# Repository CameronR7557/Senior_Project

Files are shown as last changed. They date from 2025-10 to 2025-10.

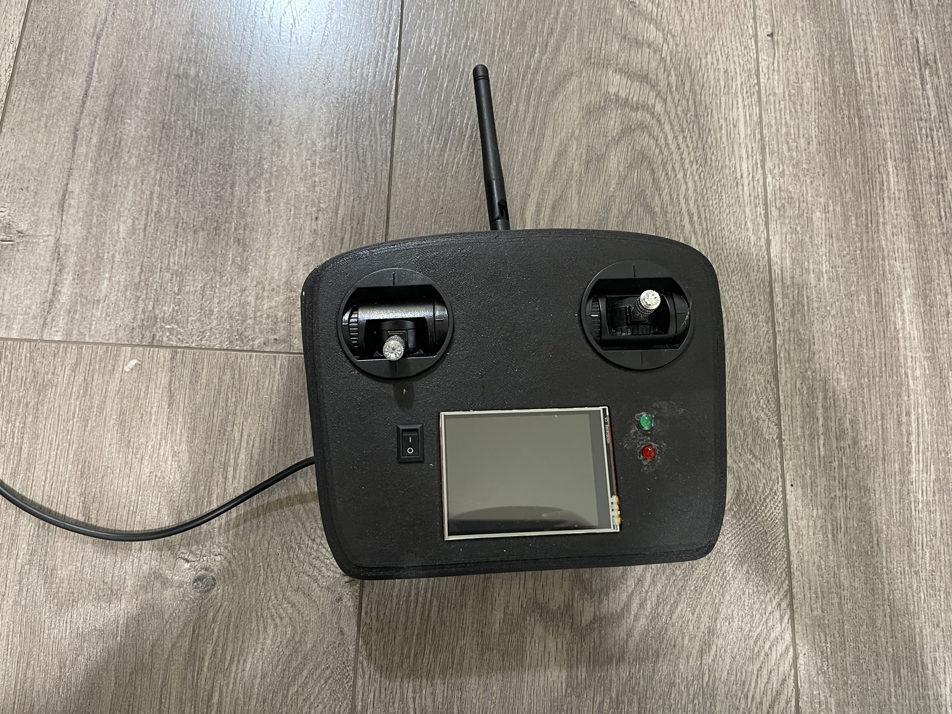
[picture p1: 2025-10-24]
Remote Control.jpg

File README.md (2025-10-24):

This repo contains the code, schematics, diagrams, etc. from my senior project in 2024. In this project I researched and prototyped a quadcopter and remote control. The goal of this project was to learn about quadcopters, LiDAR, and collision avoidance algorithms. The quadcopter used a 2D LiDAR to determine its distance from obstacles and then used those distances to update the motor control and attempt to avoid them.
It is important to note that, while I certainly learned a lot from this project, due to time constraints I was not able to get the flight controller tuned before the project ended, and was not able to test the collision avoidance algorithm on the drone in flight since the drone could not stay in the air without flipping for more than a few seconds. 

This was my planned schedule for this project.
Schedule

Below is the parts list for this project.
Parts List

This is the assembed quadcopter.

Quadcopter

This is the assembled remote control.

Remote Control

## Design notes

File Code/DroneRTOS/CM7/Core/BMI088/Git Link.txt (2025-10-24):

https://github.com/bao-eng/BMI088-STM32/tree/master

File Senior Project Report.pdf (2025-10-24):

# Senior Project Report: Collision Avoidance Drone

2024

Submitted to: Ganghee Jang

Submitted by: Cameron Robinson

June 13, 2024

Version 1.6

Submitted in fulfillment of requirements for Embedded Senior Project (CST 473), Oregon Institute of Technology.

©2024, Cameron Robinson, All Rights Reserved.

## Revision History

Version | Date | Editor | Changes
1.0 | 5/26/23 | Cameron Robinson | Initial submission for Spring of 2023
1.1 | 6/14/23 | Cameron Robinson | Revised submission for Spring of 2023
1.2 | 11/12/23 | Cameron Robinson | Updated report for middle of Fall 2023
1.3 | 12/12/23 | Cameron Robinson | Updated report for end of Fall 2023
1.4 | 2/28/24 | Cameron Robinson | Updated report for middle of Winter 2024
1.5 | 3/17/24 | Cameron Robinson | Updated report for end of Winter 2024
1.6 | 6/13/24 | Cameron Robinson | Added final sections. Revised all other sections.

## Legal Notice

The following parties have reviewed and agreed to the terms presented in this proposal.

Student:

______________________________________________________

Name | Date

Professor:

______________________________________________________

Name | Date

## Abstract

The following paper is a report on the previously proposed project to design and build a collision

avoidance quadcopter drone. Development for this project began in fall 2023 and will end in spring

2024. The estimated non-recurring costs for one engineer to work on this project 15-20 hours a week for

33 weeks is about $26,717.14 ($45.00/hour and $729.64for parts). In addition to skills such as time

management and researching, this project will require the engineer to be able to design an embedded

system; code in C; be able to design and print 3D models; and be able to design and build electric

circuits.

The purpose of this project is to research LiDAR, drone, and autonomous vehicle technologies by

creating a project that incorporates all three of them. This project is a quadcopter drone that uses a

LiDAR sensor to detect obstacles in the surrounding environment. If the drone senses it is going to

collide with any obstacles, it will automatically avoid it. The project will also include a remote control to

manually control the drone. This project is not intended to solve a particular problem or become a

sellable product.

The following paper will include details related to the major components of the project. These details

include system design, hardware, software, project requirements, testing results, and encountered

problems.

Overall, the project turned out well, and nearly all the requirements were completed and tested.

Unfortunately, the drone is still unable to fly due to destabilization in the flight controller. Despite this, a

lot was learned about collision avoidance algorithms, quadcopters, LiDARs, and flight control software

throughout the development of this project.

## Table of Contents

Inertial Measurement Unit | 22
Extended Kalman Filter | 23
PID Controllers | 23
Electronic Speed Controller | 23
BLDC Motors | 24
Project Housing | 24
Hardware | 25
Part Matrices | 26
Hardware Components | 32
Software | 40
Remote Control | 40
Quadcopter | 46
Encountered Problems | 58
Assembled Project | 59
Testing | 61
Conclusion | 63
Glossary | 65
Appendix | 66
References | 77

## List of Figures

Figure 1: Project Timeline | 8
Figure 2: Remote Control System Block Diagram | 20
Figure 3: Drone System Block Diagram | 21
Figure 4: Controller Shell | 24
Figure 5: Quadcopter Frame | 25
Figure 6: IMU Specifications Adapted from [15] | 35
Figure 7: Temperature and Pressure Conversion Equations Adapted from [13] | 36
Figure 8: Controller Software Diagram | 40
Figure 9: Blink Task Code | 41
Figure 10: ADC Conv. Complete ISR UML | 42
Figure 11: LCD Display Task UML | 43
Figure 12: LCD Task Code | 43
Figure 13: Radio RX/TX ISR UML | 44
Figure 14: Controller Radio ISR Code | 45
Figure 15: Radio Write Ack Payload Function | 45

Figure 16: Drone Software Diagram | 46
Figure 17: 2D LiDAR Task UML | 47
Figure 18: LiDAR Get Measurements Function | 48
Figure 19: Radio RX ISR | 49
Figure 20: Radio TX Task UML | 49
Figure 21: Drone Radio TX Task Code | 50
Figure 22: Collision Avoidance Algorithm Diagram | 51
Figure 23: Collision Avoidance Task UML | 52
Figure 24: Collision Avoidance Task Code | 53
Figure 25: Read IMU Task | 54
Figure 26: Read Pressure Sensor Task | 55
Figure 27: Read Pressure Sensor Task Code | 55
Figure 28: Height Task UML | 56
Figure 29: PID Update Task UML | 58
Figure 30: Assembled Quadcopter Drone | 59
Figure 31: Assembled Controller - Top-Down | 60
Figure 32: Assembled Controller – Front | 60
Figure 34: Controller Wiring Schematic | 66
Figure 35: Drone Wiring Schematic | 67
Figure 35: LiDAR Data Parsing Function | 68
Figure 36: LiDAR CRC Function | 69
Figure 37: ADC Conversion Complete ISR | 70
Figure 38: PID Control Equations. Adapted from [5] | 71
Figure 39: IMU Task | 72
Figure 40: Drone Radio RX ISR | 73
Figure 41: Rangefinder Functions | 74
Figure 42: Init CA and Obstacle Detection Functions | 75
Figure 43: Obstacle Avoidance Function | 75
Figure 44: Measure Height Task Code | 76

## List of Tables

Table 1: Estimated Engineering Costs | 9
Table 2: Estimated Cost of Parts | 10
Table 3: Potential MCUs | 27
Table 4: Potential IMUs | 27
Table 5: Potential Pressure Sensors | 28
Table 6: Potential ESCs | 28
Table 7: Potential Radio Transceivers | 29
Table 8: Potential LCDs | 29
Table 9: Potential Rotating LiDARs | 30
Table 10: Potential BLDC Motors | 31
Table 11: Potential LiPo Batteries | 32
Table 12: Potential Distance Measuring Units | 32

## Project Management

### Project Timeline

Figure 1, pictured below, is the timeline of the collision avoidance quadcopter drone project. The blue

tasks will be done by the end of winter 2024. The purple tasks represent project stretch goals; they may

or may not be implemented during spring of 2024. There were a couple of delays throughout the

development of this project. The first delay was due to the IMU data not being filtered enough, which

caused the accelerometer readings to spike to very large values. The second, and most significant delay,

was due to the drone’s flight controller destabilizing and causing the drone to oscillate out of control.

Due to these delays, it is unlikely that the stretch goals will be implemented during spring term.

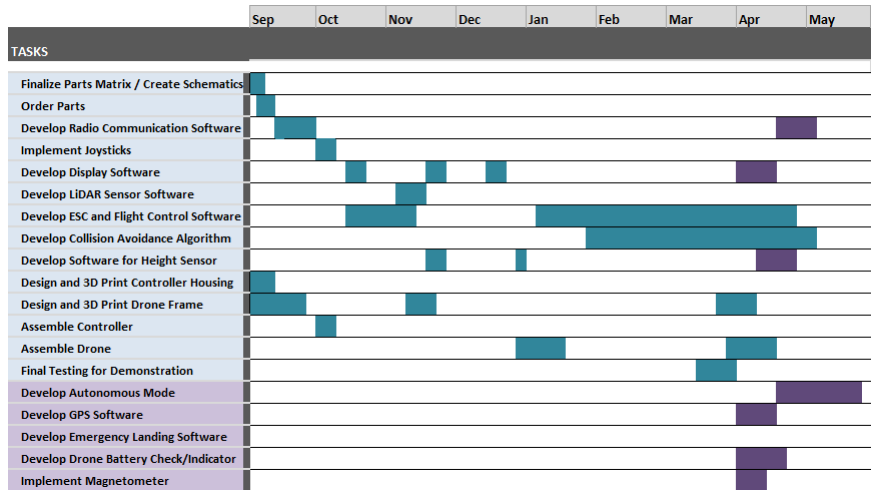
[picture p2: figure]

Figure 1: Project Timeline

### Non-Recurring Costs

The cost of one engineer working on this project for 15 – 20 hours a week at $45.00 per hour is about

$787.5 dollars per week. The total amount of time for initial development is about 22 weeks (fall 2023

and winter 2024), which results in a cost of $17,325.00. The total time for testing and developing

additional features is about 11 weeks (Spring 2024) which results in an additional cost of $8,662.50.

Table 1 shows the estimated engineering costs for fall, winter, and spring, as well as the total estimated

engineering cost. Table 2 lists all the parts and materials used in the project and how much they cost.

The total estimated cost of all parts is $729.64. Overall, the total estimated non-recurring cost for

research and development over a 33-week period is $25,987.50 in engineering costs and $729.64 in

materials, which results in a total cost of $26,717.14.

Table 1: Estimated Engineering Costs

Reason | Cost ($)
Fall Term Research and Development (11 Weeks) | 8,662.50
Winter Term Development (11 Weeks) | 8,662.50
Spring Term Testing and Development (11 Weeks) | 8,662.50
Total: | 25,987.50
Part Name | Quantity | Unit | Total Part Cost ($)
NUCLEO-H755ZI-Q | 2 | pcs | 58.00
Grove 6-Axis IMU (BMI088) | 1 | pc | 29.04
ICP-10111 Pressure Sensor | 1 | pc | 7.90
F405 V3 50A 4in1 ESC | 1 | pc | 49.99
NRF24L01+PA+LNA w/ Breakout Adapter | 3 | pcs | 13.99
ILI9341 2.8" SPI TFT LCD | 1 | pc | 16.39
FHL-LD19 | 1 | pc | 84.34
2212 920KV BLDC Motor | 4 | pcs | 39.99
HRB 4S LiPo | 1 | pc | 37.49
LIDAR07 | 1 | pc | 19.99

### Project Tools

GitHub, Word, and Excel will be the primary project management tools used in this project. GitHub will

be used for source control and storing documentation, and diagrams. Word will be used for

documentation development and storing research notes. Excel will be used to create graphs, tables, and

charts (such as Gantt charts) that will be used for project management.

Onshape, a CAD program, will be used for designing the 3D parts for both the drone and controller. As a

student, Onshape is free to use, so using it does not add to the cost of the project.

Other tools that will be used throughout this project include Dia and KiCad. Dia will be used to create

project diagrams (such as system block diagrams), and KiCad will be used to make wiring schematics.

Other software tools, such as IDEs, are discussed under the ‘Software’ heading in the ‘System

Description’ section.

1045 Propellers | 4 | pcs | 15.99
NylonG | 1000 | g | 128.00
NylonX | 500 | g | 58.00
Rosin Core Lead-Free Solder | 100 | g | 19.99
URGENEX 7.4V LiPo | 2 | pcs | 19.99
SCIGRIP Acrylic Plastic Cement | 5 | fl. oz. | 14.35
14 AWG Silicone Wire | 50 | ft | 19.98
Dupont Wires | 120 | pcs | 6.98
LM7805 | 2 | pcs | 8.29
Rocker Switch | 1 | pc | 6.99
Joystick | 2 | pcs | 31.98
LEDs | 2 | pcs | 0.05
330-Ohm Resistors | 2 | pcs | 0.06
LM2596 Buck Converter | 4 | pcs | 13.99
1045 Carbon Fiber Propellers | 8 | pcs | 27.88
Total Estimated Parts Cost | | | 729.64

Table 2: Estimated Cost of Parts

### Change Management Procedure

Any changes to this project after the beginning of fall 2023 will require the engineer to submit a request

for that change in the form of an Engineering Change Order (ECO). The ECO form should contain

information about what change is being made, why it is being made, and what will be affected by the

change. The engineer must submit the ECO and get it approved by their supervisor. Changes to the

project may require additional forms to be filled out or previously submitted work to be revised or

recreated.

### Status Report

The engineer in charge of the project will be required to submit a weekly memo to their supervisor. This

memo will contain:

- Project progress
- Updates to the timeline
- Problems encountered
- Goals for the following week
- Any major problems or setbacks

Should the engineer fail to submit the weekly memo, there will be repercussions.

### Skills

This project will require the following skills:

- Programming in C
- Designing system diagrams and wiring schematics
- Soldering
- Designing and printing 3D models

- Researching and understanding complex topics (drone flight, PID control, collision avoidance

algorithms, etc.)

- Managing time and workload
- Ability to solve complex problems
- Ability to test hardware and software on embedded systems

## Conceptual Overview

### Introduction

Technology tends to advance very quickly, with new technologies constantly being released and the

applications of existing technologies expanding. This is also the case with technologies such as LiDAR,

drones, and autonomous vehicles. Fields that LiDAR is used in include agriculture, construction,

geographical mapping, and autonomous vehicles. Drones, in addition to being used in agriculture and

geographical mapping, are also used in weather and storm monitoring, cinematography, and much

more. Autonomous vehicle technologies like autonomous delivery drones and cars are also constantly

advancing.

The project outlined in this paper is a research project that combines these three technologies: drones,

LiDAR, and autonomous vehicle algorithms. The purpose of this project is to learn about these

technologies and gain a better understanding of them. Although this project is not going to solve a

particular solution in a completely unique way, it is still a valuable project because drones, LiDAR and

autonomous vehicles are advancing technologies with a multitude of applications.

### Intended Audience

Since my project is a research project, my primary audience is academics. Particularly, any person

wanting to learn more about LiDAR, drones, and collision avoidance algorithms.

### Proposed Project

This document is a proposal to create a collision avoidance quadcopter drone. The main components of

this project are a quadcopter, remote control, and collision avoidance algorithm. For collision avoidance

the drone will use a 2D 360-degree rotating LiDAR. This module will sit on the drone and constantly

measure the distance between the drone and obstacles in the surrounding environment. These distance

measurements will be used by collision avoidance algorithms to adjust the drone’s flight to avoid any

obstacles it will collide with. The remote control will be used to manually control the flight of the drone

with two joysticks.

### Existing Solutions

Quadcopters

There are multiple collision avoidance drones currently on the market. The cost of these drones tends to

range from around $300.00 to well over $1000.00. Two example drones are the DJI Air 2S [1] and the

EXO X7 Ranger PLUS [2]. Although neither of the drones’ product pages specify what kind of sensor

(LiDAR, ultrasonic, etc.) each drone uses, neither one appears to use a 2D 360-degree rotating LiDAR

sensor. Additionally, although the EXO X7 Ranger PLUS does have 360-degree obstacle detection, it

avoids obstacles by simply stopping the drone, rather than flying around the obstacle.

Collision Avoidance Algorithm

The collision avoidance algorithm developed throughout this project shares some similarities to the

dynamic window approach (DWA) [21]. The DWA is a collision avoidance algorithm that analyzes a small

area around a robot and determines the path the robot should take by considering its velocity and the

location of surrounding obstacles. The area around the robot that is analyzed, the dynamic window, is

determined by how far the robot can travel given its restrictions and velocity. This algorithm is an

example of a dynamic collision avoidance algorithm because it reacts to obstacles without prior knowledge of the environment. In this project, the collision avoidance algorithm will be a dynamic

algorithm, however, it will not implement any form of path planning like the DWA.

Flight Controller

There are many methods of implementing flight controllers for quadcopters, however, one of the most

common methods uses a 6-axis inertial measurement unit (IMU) and PID controllers. Often, the PID

controllers are implemented to control the angle and angular rate of the quadcopter.

The IMU data is used as measurement inputs into the PID controllers. Measurement inputs represent

the current state of the drone. For example, a flight controller could have three angular rate controllers

(one for roll rate, pitch rate, and yaw rate), where each controller receives its respective angular rate

measurement from the IMU’s 3-axis gyroscope that represents how fast the drone is currently rotating

on that specific axis.

The PID controllers also receive a setpoint value, which represents the state they are controlling to. In

most quadcopters, the setpoint for each axis is determined by the position of the joysticks on the remote

control. PID controllers calculate output values based on an error term, which is the difference between

the setpoint and the measurement (the difference between the current state and the desired state).

These outputs are used in motor-mixing equations to calculate throttle values for each of the

quadcopter’s motors that will get the drone from its current state to its desired state.

### Deliverables

The final deliverables of this project will be a mostly functional remote control and quadcopter drone as

specified in the ‘Requirements’ section. The controller will control the flight of the drone with two

joysticks. The drone will incorporate a LiDAR module which it will use to detect obstacles in the

surrounding environment. The drone will attempt to avoid obstacles it is going to collide with. The

project should be mostly functional by the end of spring 2024.

## Requirements

The following is a list of requirements for the collision-avoidance quadcopter drone. These requirements

define what the final project should be able to do by the end of Spring 2024. Under each requirement is

a list of the identification numbers of codependent requirements. The listed codependent requirements

are requirements that are essential to the completion of the requirement they are listed under.

1. The project will have a quadcopter drone with four propellers, each rotating on a brushless DC

motor.

a. The motors and propellers will be used by the drone to maneuver in the air.
b. The drone will be custom-built for this project.

Codependent requirements: 3, 5.

2. The project shall have a remote control to operate the drone from a distance.
a. The controller will be custom-built for this project.

Codependent requirements: 1, 3, 4, 7.

3. The drone and controller will both have their own microcontrollers.
a. Each microcontroller shall be fast enough to process all needed data and respond to

external events in near real-time.

Codependent requirements: 1, 2, 5.

Justification: This project will use microcontrollers for both the controller and drone since most

commercial quadcopters use them. Near real-time responses will be essential for avoiding obstacles.

4. The drone and controller will communicate via radio.
a. May be able to communicate from 50 feet away.

b. Shall be able to communicate from 25 feet away.

Codependent requirements: 1, 2, 3, 5.

5. The drone and controller will be powered by batteries.
a. The batteries will be rechargeable.
b. The drone may be able to fly for 15 minutes or more.

Codependent requirements: 1, 2.

6. The controller will have an LCD screen to display relevant information related to the drone.
a. The LCD screen shall display indications of obstacles around the drone.
b. The LCD screen may display the drone’s GPS location data.
c. The LCD screen shall refresh at least 15 times per second.
d. The LCD screen may indicate quadcopter battery level.

Codependent requirements: 2, 4, 8.

7. The controller will have two joysticks.
a. One joystick will control the throttle and yaw of the drone.
b. One joystick will control the pitch and roll of the drone.
c. The values of each joystick will be read through an ADC on the controller’s MCU.

Codependent requirements: 1, 2, 3, 4.

8. The drone shall use a rotating LiDAR module for obstacle detection.
a. LiDAR module will be active while the drone is in flight.
b. The module shall detect objects at least three meters away.
c. The module may detect objects up to twelve meters away.

Codependent requirements: 1, 3, 5.

Justification: One of the main goals of this project is to learn about LiDAR, so while something like an

ultrasonic sensor may fulfill a similar purpose, a LiDAR is more in line with the goals of this research

project. The LiDAR should be able to detect obstacles at least three meters away since that will

hopefully give the drone enough time to stop or avoid it, however, due to restrictions on LiDAR

resolution, some small objects may be missed even at distances closer than three meters.

9. The drone shall use an inertial measurement unit (IMU) to increase flight stability.
a. The IMU data shall be used to adjust the speed of the drone’s motors.
b. The IMU will have at least a 3-axis gyroscope and 3-axis accelerometer.

Codependent requirements: 1, 3, 5.

10. The drone shall attempt to avoid detected obstacles if it senses it is going to collide with any.
a. Results from object detection algorithms shall be used along with drone movement data

(i.e., from IMU and joysticks) to determine if the drone will collide with an obstacle.

b. The movement of the drone shall be adjusted to prevent collision with obstacles.

Codependent requirements: 1, 2, 3, 4, 5, 7, 8, 9.

11. The drone may have an autonomous mode.
a. In autonomous mode, the drone may take off, fly to a specified location, avoid obstacles,

and land on its own.

b. Autonomous mode may be turned on and off with a switch on the controller.

Codependent requirements: 1, 3, 5, 8, 9, 10, 13, 14.

Justification: As discussed later in the ‘Part Matrices’ section, the quadcopter will use an H7-series

STM32 microcontroller. Many commercial quadcopter drones, even those with GPS return-home functions, use F4 or F7-series STM32 MCUs. The F-series MCUs have less than half the maximum

clock speed of the H7-series, which makes it seem feasible that an autonomous mode could be

implemented in this project.

12. The drone shall have a semi-autonomous mode.
a. In semi-autonomous mode, the drone’s flight shall be controlled with the controller.
b. In semi-autonomous mode, the drone shall automatically detect and attempt to avoid

obstacles it senses it will collide with.

c. Semi-autonomous mode may be turned on and off with a switch.

Codependent requirements: 1, 2, 3, 4, 5, 7, 8, 9.

13. The drone will use a distance measuring module to measure its distance from the ground.
a. The module will either be a LiDAR or ultrasonic ranging module.
b. The module’s distance measurements may be used to make the drone hover some

distance above the ground.

c. The module’s distance measurements may be sent to the controller to display on the

LCD.

Codependent requirements: 1, 3, 5.

Justification: Knowing how far the drone is from the ground will allow for better obstacle avoidance

since the drone may need to know if it can fly up or down to avoid an obstacle. Either a LiDAR or

ultrasonic ranging module could fulfill this purpose.

14. The drone will use a pressure sensor to estimate its distance from the ground.
a. The pressure sensor may be used in conjunction with the distance sensor to get a more

accurate measurement of how far the drone is from the ground.

Codependent requirements: 1, 3, 5.

Justification: A pressure sensor fulfills the same role as the distance sensor mentioned in

requirement 13, however, it can measure much further distances from the ground than the distance

measuring module. If used alongside the distance measuring module, the estimated distance from

the ground should be more accurate than just using one or the other.

15. The drone may use a GPS module to receive data related to its own location.
a. GPS data may be used to allow the drone to fly to a specific location.

Codependent requirements: 1, 3, 5.

16. The drone may have an emergency landing feature where the drone will automatically land on

the ground.

a. An emergency landing may initiate when the battery reaches a certain level.
b. An emergency landing may initiate if the drone loses connection with the controller.

Codependent requirements: 1, 3, 5.

17. Most parts of the drone and controller’s housing shall be 3D printed.

Codependent requirements: 1, 2.

## System Description

The following section is an overview of the system designs for remote control and drone, which are

designed to meet the above requirements.

### Remote Control

Figure 2, pictured below, illustrates the system block diagram for the remote control. The main

components in the controller are the analog to digital converter (ADC), radio transmitter (Radio TX),

radio receiver (Radio RX), display, and the two joysticks.

ADC and Radio TX:

The ADC is used to read the positions of the two connected joysticks. In total, the ADC will read four

values from the joysticks; throttle and yaw from one joystick, and pitch and roll from the other. These

values are used to control the angular velocity of the drone’s four motors. Once the data is collected

from the joysticks, it is sent to the radio transmitter which will transmit it to the drone’s radio receiver.

Radio RX and LCD

The radio receiver receives LiDAR data from the drone and sends it to the LCD, which will display

detected obstacles within a certain distance from the drone.

Figure 2: Remote Control System Block Diagram

### Quadcopter Drone

Figure 3, shown below, illustrates the system block diagram for the drone. The major components

include the radio transmitter and receiver, 2D LiDAR, rangefinder, inertial measurement unit, extended

Kalman filter, PID controllers, brushless DC (BLDC) motors, electronic speed controller (ESC), pressure

sensor, and collision avoidance algorithm.

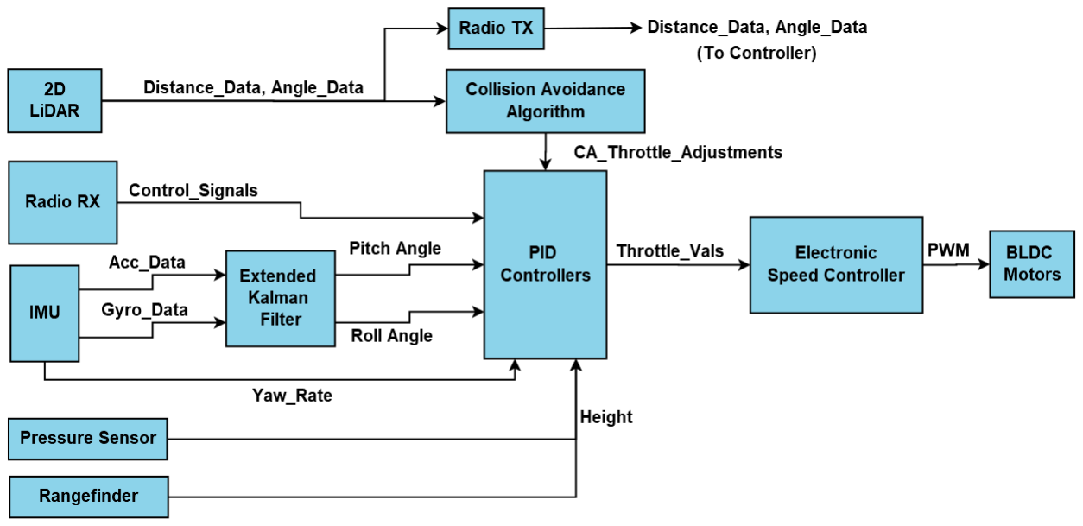
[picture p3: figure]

Figure 3: Drone System Block Diagram

2D LiDAR

The 2D LiDAR module is a 360-degree rotating distance sensor that measures distances between the

drone and obstacles in the surrounding environment. This distance data is sent to the Radio TX and

Collision Avoidance Algorithm blocks.

Rangefinder and Pressure Sensor

Both the rangefinder and pressure sensor perform the same function: they measure the distance

between the drone and the ground. This data will potentially be used to allow the drone to hover a

certain height above the ground. Not only does measuring the distance to the ground with two different

sensors help verify that the measurements are correct, but each sensor also helps account for the

other’s weaknesses. The rangefinder is only accurate when measuring certain types of materials and can

only measure up to a maximum distance. On the other hand, the pressure sensor is not restricted by distance from the ground, however, its measurements are based on the air pressure at sea level, so it

does not necessarily know how far away the ground is.

Radio TX

The radio transmitter sends the LiDAR angles and distance measurements to the remote control.

Collision Avoidance Algorithm

The collision avoidance algorithm for this project uses the 2D LiDAR data to detect obstacles in the

drone’s surroundings. This algorithm is divided into three steps: obstacle detection, hazard assessment,

and obstacle avoidance.

Obstacle detection analyzes the LiDAR data to determine the distance and direction of obstacles around

the drone. The hazard assessment step determines which obstacles the drone is most likely to collide

with and outputs values that prioritizes avoiding those obstacles. Lastly, obstacle avoidance uses the

results from the hazard assessment and obstacle detection stages to determine adjustment values for

the drone’s motors that will allow it to avoid the obstacles.

Radio RX

The radio receiver receives joystick position data from the remote control. This data is sent directly to

the PID Controllers block.

Inertial Measurement Unit

The inertial measurement unit (IMU) is a sensor that detects linear acceleration and angular velocity.

This module is essential to the flight controller since it provides angle and angular rate measurements to

the PID controllers. Angular velocity is measured with a 3-axis gyroscope and linear acceleration is

measured with a 3-axis accelerometer. The gyroscope and accelerometer readings are sent to the

Extended Kalman Filter block. The gyroscope yaw reading is also sent directly to the PID Controllers

block.

Extended Kalman Filter

The extended Kalman filter is implemented in software and uses the gyroscope and accelerometer data

to estimate the quadcopter’s roll and pitch angles. The roll and pitch angle estimations are sent to the

PID Controllers block and are used for controlling and the drone’s flight.

PID Controllers

The PID Controllers block represents software algorithms for controlling drone flight and stabilization.

This block takes in the joystick data, collision avoidance results, IMU data, and the drone’s distance from

the ground. This data is used to calculate how fast each of the drone’s four motors should be spinning to

avoid obstacles or move in the direction specified by the joystick values. Once the throttle for each

motor is calculated, the values are sent to the ESC through a protocol called DSHOT.

In general, the data will be used as follows:

- The joystick data will control the drone’s orientation and throttle (PID setpoint).
- The IMU data will provide the measured orientation of the drone (PID measurement).
- The results from the collision avoidance algorithm will adjust the drone’s flight to avoid obstacles

(also a PID setpoint).

- The drone’s measured height may be used to hover the drone a set distance above the ground

(not currently implemented).

Electronic Speed Controller

The ESC receives data through a protocol called DSHOT. There is one communication line for each of the

four motors, which allows each of the motors’ throttles to be changed independently.

BLDC Motors

The BLDC motors are what enable the quadcopter to fly. These motors are controlled through the ESC.

The angular velocity of each motor determines the net thrust on the drone which controls all

movements of the drones.

### Project Housing

Figure 4 shows the 3D model for the remote control. The face of the controller shell has cut-outs for the

joysticks, LCD, two LEDs, and a power switch. The front of the controller has cut-outs for the battery and

radio antenna.

Figure 4: Controller Shell

Figure 5 is a 3D model of the quadcopter frame. The frame measures about 445mm on the diagonal (not

including the bumpers) and weighs about 500g. All the components, aside from the BLDC motors, are designed to fit on or within the central container. The rectangular hole in the top of the frame is for the

2D rotating LiDAR. The LiDAR is designed to stick out above the rest of the frame so that it can measure

360-degrees around the drone. Each BLDC motor sits on one of the four corners of the frame. The

circular bumpers around the frame are intended to minimize the damage caused by collisions that may

occur during testing.

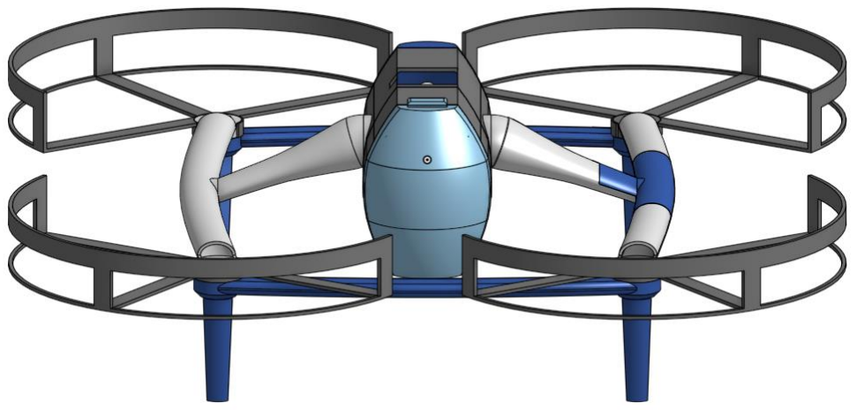
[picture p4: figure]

Figure 5: Quadcopter Frame

The housing for both the drone and controller were made using Onshape.

### Hardware

The controller will have six hardware components. These components include an MCU, radio transceiver,

LCD display, two joysticks, and a rechargeable battery. The MCU will either need multiple ADCs or one

ADC with multiple channels to read the positions of each joystick. Additionally, the MCU will need pins

for some serial protocols in order to communicate with the radio and LCD display.

The hardware components for the drone include:

- An MCU
- Four BLDC motors

- One 6-axis IMU
- A radio transceiver
- LiDAR module
- Distance measuring unit (ultrasonic or LiDAR)
- Pressure sensor
- Rechargeable battery (LiPo or Li-ion)
- Electronic speed controller (ESC)

The MCU will need enough serial protocol pins to communicate with each of the peripheral devices. The

MCU will also need four pins capable of outputting DSHOT or PWM signals for sending data to the ESC.

The battery needs to be able to supply enough current to run all the motors at full power and it must be

able to power the normal functions of the drone for 15 minutes.

Part Matrices

The following tables are part matrices for the core components of the project described above. Each

table specifies at least three potential components that could be used. The components highlighted in

green are the ones chosen for this project.

Table 3 illustrates potential MCUs that would work for both the quadcopter and controller. The board

chosen for this project was the NUCLEO-H755ZI-Q. Although this board has a lower clock speed than the

Pi boards, it has far more GPIO pins and serial communication pins; both of which will be extremely

useful for this project since there are multiple peripheral sensors and motors. The NUCLEO board also

takes far less power than the Pi boards which will help extend the battery life of the quadcopter. The

need for an MCU is directly connected to the third requirement in the ‘Requirements’ section.

MCUs
Module Name | NUCLEO-H755ZI-Q | Raspberry Pi 4 | Raspberry Pi Zero W | NanoPi M4B
Cost ($) | 29.00 | 82.00 | 15.00 | 119.99
CPU Speed | 480MHz | 1.5GHz | 1GHz | 2.0GHz
RAM | 1MB | 4GB | 512MB | 2GB
Flash | 1MB | Micro SD | Micro SD | Micro SD
Relevant Serial Protocols (I2C, SPI, UART, etc.) | 4x I2C, 4x UART, 1x LPUART, 6x SPI | 1x I2C, 1x UART, 1x SPI, 2x USB 2.0, 2x USB 3.0 | 1x I2C, 1x UART, 1x SPI | 2x USB 2.0, 2x USB 3.0, 3x I2C, 1x UART, 1x SPI
GPIO | 144 pins | 40 Pins | 40 Pins | 64 pins
Other | 3.3V/0.5A (max) | 5V/3A | 5V/2.5A | 5V/3A
Table 3: Potential MCUs

Table 4 shows several options for the quadcopter’s inertial measurement unit (IMU). The IMU chosen for

this project was the BMI088. The primary reason for this decision was that the BMI088 was designed

specifically for quadcopters and other drones, so although it is not the cheapest option, it will hopefully

be the best performing one. The IMU is necessary to fulfill requirement nine.

Inertial Measurement Unit
Module Name | Grove 6-Axis IMU (BMI088) | GY-87 10DOF Module | BNO055+BMP280 10DOF Module | Fermion: 10DOF IMU Sensor
Cost ($) | 29.04 | 16.99 | 25.90 | 39.50
Accelerometer | 3-Axis | 3-Axis | 3-Axis | 3-Axis
Gyroscope | 3-Axis | 3-Axis | 3-Axis | 3-Axis
Magnetometer | No | 3-Axis | 3-Axis | 3-Axis
Pressure Sensor | No | Yes | Yes | Yes
Communication Protocol | I2C | I2C | I2C | I2C
Other Notes | Designed specifically for drones. | | Also has temperature sensor | Also has temperature sensor

Table 4: Potential IMUs

Table 5 shows options for pressure sensors, which are needed because the BMI088 does not have one.

Any of the listed devices would work and none of them are very expensive. The device chosen for this

project was the Ferimon ICP-10111 pressure sensor since it was designed specifically for drones, and it

has the highest relative accuracy. A pressure sensor is needed to fulfill requirement 14.

Pressure Sensors
Module Name | Ferimon ICP-10111 | BME280 Altimeter | BMP390
Cost ($) | 7.90 | 9.98 | 14.99
Communication Protocol | I2C | I2C/SPI | I2C/SPI
Relative Accuracy | +/- 1 Pa | +/- 12 Pa | +/- 3 Pa
Other Notes | Intended for drones. | Specifies “flying toys” as a target device. Also has a humidity sensor.

Table 5: Potential Pressure Sensors

Table 6 illustrates various electronic speed controllers (ESC) to control the quadcopter’s BLDC motors.

The ESC chosen for this project was the SpeedyBee F405 V3 50A 4-in-1 ESC since it has a good balance

between firmware and cost. Although the Hobbypower and QWinOut ESCs are both cheaper, they use

SimonK firmware, which is outdated. These ESCs are also bulkier than the other three options since they

are not 4-in-1 ESCs. The HolyBro and T-Motor boards have the newest firmware, however, they are

nearly double the cost of the SpeedyBee ESC and the increase in performance does not justify the extra

cost. The need for an ESC is directly connected to requirement one.

Electronic Speed Controllers
Module Name | Hobbypower SimonK 30A ESC Brushless Speed Controller BEC 2A | QWinOut 2-4S 30A RC Brushless ESC Simonk Firmware Electric Speed Controller | SpeedyBee F405 V3 50A 4in1 ESC Board | HolyBro Tekko32 F4 | T-Motor F55A Pro
Cost ($) | 35.99 | 38.00 | 49.99 | 106.91 | 90.90
Firmware | SimonK | SimonK | BLHeli_S | BLHeli32 | BLHeli32
Amp Rating (A) | 30 | 30 | 50 | 60 | 55
Amount | 4 | 4 | 1 | 1 | 1
Other | Controlled through PWM | | 4-in-1. Uses DSHOT300/600 protocol. | 4-in-1. Supports nearly all protocols (PWM, DSHOT, etc.). | 4-in-1. Supports nearly all protocols. (PWM, DSHOT, etc.).

Table 6: Potential ESCs

Table 7 shows three options for radio transceivers that would work for communication between the

controller and quadcopter. This project will use the NRF24L01+PA+LNA simply because there are already

some on hand, which makes the cost of the part effectively zero. Additionally, when compared to the

other NRF24L01+, the NRFL01+PA+LNA has a much larger external antenna which should allow it to

transmit further distances. A radio transceiver is necessary to fulfill requirement number four.

Radio Transceivers
Module Name | NRF24L01+PA+LNA Wireless Transceiver RF Transceiver Module + Breakout Adapter | NRF24L01+ (Integrated Antenna) | ExpressLRS ELRS EP1 TCXO Long Range Low Latency Receiver
Cost ($) | 13.99 | 11.99 | 22.99
Amount | 3 | 10 | 1
Frequency (GHz) | 2.4 | 2.4 | 2.4
Communication Protocol | SPI | SPI | UART

Table 7: Potential Radio Transceivers

Table 8 shows three options for the controller’s LCD display. All the options are fairly cheap and all of

them use SPI to communicate, so the primary deciding factor was the size of the LCD since it needs to be

able to clearly display obstacles surrounding the quadcopter. For this reason, the HiLetgo ILI9341 2.8”

TFT LCD was chosen since it has a 0.8” larger screen than the Waveshare IPS LCD. An LCD is needed for

requirement six.

LCD Displays
Module Name | Waveshare General 2inch IPS LCD Display | 1.8" SPI TFT LCD Display | HiLetgo ILI9341 2.8” SPI TFT LCD
Cost ($) | 14.65 | 11.37 | 16.39
Resolution | 240x320 | 128x160 | 240x320
Driver | ST7789 | ST7789 | ILI9341
Serial Protocol | SPI | SPI | SPI
Other | IPS Display
Table 8: Potential LCDs

Table 9 illustrates the various LiDAR modules for obstacle detection. The main considerations were the

cost, samples per second, mass, and ability to function in sunlight (lux rating). In the end, the LiDAR chosen for this project was the FHL-LD19. Although this LiDAR has the lowest sample rate, it also has the

lowest cost, and lowest mass. Even with the low sample rate, the LiDAR should still be fast enough to

detect most obstacles, however, if the object is too small, the LiDAR may miss it from further distances,

which means the quadcopter will have less time to react. Overall, it was difficult to justify using an

expensive LiDAR on a quadcopter that will likely collide with multiple walls throughout the development

of the collision avoidance and flight controller software. A 2D LiDAR module is needed to fulfill

requirement eight.

2D LiDAR Modules
Module Name | RPLIDAR A2M12 | RPLIDAR A1M8-R6 | youyeetoo FHL-LD19 Lidar Sensor | RPLiDAR S2L
Cost ($) | 229.00 | 99.00 | 84.34 | 299.00
Range (m) | 0.2 - 12 | 0.2 - 12 | 0.2 - 12 | 0.05 - 18
Communication Protocol | UART | UART | UART | UART
Samples Per Second | 16k | 8k | 4.5k | 32k
Rotation Frequency (Hz) | 5 - 15 | 5.5 | 5 - 13 | 10
Lux Rating | Doesn’t Specify | Doesn’t Specify | 30k | 80k
Mass (g) | 170 | 170 | 50 | 190
Other | Needs PWM. Triangulation. | Needs PWM. Triangulation. | Needs PWM. Time of Flight. | Doesn’t appear to need PWM. Time of Flight.

Table 9: Potential Rotating LiDARs

Table 10 shows three of the options for BLDC motors. The main consideration for the motors was the KV

rating. The quadcopter in this project will be relatively large, so a motor with a lower KV rating is most

preferable since it will work better with larger propellors. The higher KV motors are often catered

towards FPV racing drones which are designed to be small and light. For this reason, with the added

benefit of also being the cheapest, the 2212 920KV BLDC motors were chosen for this project. Although

the peak current of these motors is not specified, it is very unlikely to be over 50 amps which is the

rating of the SpeedyBee ESC. BLDC motors are needed to fulfill requirement one.

Brushless DC Motors
Module Name | 2212 920KV Brushless Motors | XING-E Pro 2207 1800KV Brushless Motor | XING-E Pro 2207 2450KV
Cost | 39.99 | 62.99 | 63.99
Amount | 4 | 4 | 4
Voltage (V) | 7-12 | 7.4 – 22.2 | 7.4 – 14.8
Peak Current (A) | Doesn’t Specify | 35 | 43
KV Rating | 920 | 1800 | 2450
Mass (g) | 53 | 33.8 | 33.8
Other | ~750-800g lift. Intended for DJI Phantom. | Intended to be used with a 6S battery. For FPV. | Intended to be used with 4S batteries. For FPV.

Table 10: Potential BLDC Motors

Table 11 indicates multiple options for LiPo batteries that would be used to power the quadcopter and

remote control. Most of the batteries are 14.8V (4S) since that is the most common voltage for

quadcopters and will work with the ESC and the motors. The battery chosen for the drone was the HRB

4S 4200mAh LiPo. The main considerations when choosing this battery were the mAh rating, C rating,

weight, and cost. These values were compared to the needs of the BLDC motors, which have the highest

power consumption in this project. The mAh rating was based on what was recommended for a 450mm

quadcopter with 920 KV motors. The HRB battery also has a 60C rating which means it should be able to

supply 50A to all four motors at the same time, though that much current should not be necessary. The

URGENEX 7.4V battery was chosen to power the remote control because it is small and there are already

some on hand. LiPo batteries are needed to fulfill requirement five.

LiPo Batteries
Module Name | URGENEX 7.4V Lipo Battery | Zeee 14.8V 4S Lipo Battery 50C 3300mAh | Zeee 4S Lipo Battery 5200mAh 14.8V 120C | Zeee 4S Lipo Battery 6200mAh 14.8V 80C | HRB 4S Lipo Battery 14.8V 4200mAh 60C
Cost ($) | 19.99 | 62.09 | 89.09 | 92.79 | 37.49
Amount | 2 | 2 | 2 | 2 | 1
Voltage (V) | 7.4 | 14.8 | 14.8 | 14.8 | 14.8
C Rating | 35 | 50 | 120 | 80 | 60
mAh | 1000 | 3300 | 5200 | 6200 | 4200

Max Cont. Current (A) | 35 | 165 | 624 | 496 | 252
Mass (g) | 51 | 348 | 470 | 625 | 410
Table 11: Potential LiPo Batteries

Table 12 illustrates three distance measuring sensors that could be used by the quadcopter to measure

its distance from the ground. The module chosen for this project is the LIDAR07 since it can measure

much further than the HC-SR04, and is half as expensive as the TFmini-S. Although the TFmini-S is more

accurate than the LIDAR07, it is not by much, so the extra cost does not seem justified for this project.

The distance sensor will be used in conjunction with the pressure sensor to determine the height of the

quadcopter, so an extra 0.5% accuracy is irrelevant. A distance measuring module is needed to fulfill

requirement 13.

Distance Measuring Units
Module Name | LIDAR07 (SEN0413) | HC-SR04 | TFmini-S Lidar Sensor
Cost ($) | 19.99 | 8.99 | 43.90
Type | LiDAR | Ultrasonic | LiDAR
Range (m) | 0.2 - 12 | 0.2 - 4 | 0.1 - 12
Communication Protocol | I2C/UART | Trigger-Pulse | UART/I2C
Accuracy | +/- 5cm @ 20 – 350 cm +/- 1.5% @ 351 – 1200 cm | Up to 3mm resolution | +/- 6cm @ 10 – 600 cm +/- 1% @ 601 – 1200 cm

Table 12: Potential Distance Measuring Units

Hardware Components

Figure 34 and Figure 35, shown in the appendix, are the wiring schematics for the controller and drone,

respectively. The schematics illustrate how all the components are connected to the MCUs and how they

are powered by the batteries. In general, everything but the ESC can be powered with 5V. The ESC is

powered directly from the drone’s battery which is about 14.8V. It is important to note that the radios should only be powered with 5V if using their breakout adapters, otherwise, they should be powered

with 3.3V.

NUCLEO-H755ZI-Q

The NUCLEO-H755SZI-Q is a development board used in both the drone and controller. The boards use

the STM32H755ZI microcontroller. Both NUCLEO boards are powered with LiPo batteries through their

E5V pins. The voltage supplied to each board is stepped-down to 5V with buck-converters. The clock

frequencies on the boards are set to 300MHz; the peripheral clocks are set to 75MHz; and the timer

clocks are set to 150MHz. Table 13 and Table 14 show the peripheral settings for the controller and

drone respectively. The tables contain the peripheral names, important settings, and what it is used for.

The GPIOs are not listed because they are shown in the wiring schematics found in the appendix. For

more details on the MCU, see the STM32H755xI datasheet [17].

Drone STM32CubeIDE Peripheral Settings
Peripheral | Settings | Use
DMA1 Stream 1 | Mem-to-peripheral; Request: TIM3_CH1; Data Width: Half-Word; Priority: High | ESC DShot Comm. M1
DMA1 Stream 2 | Mem-to-peripheral; Request: TIM4_CH2; Data Width: Half-Word; Priority: High | ESC DShot Comm. M2

Remote Control STM32CubeIDE Peripheral Settings
Peripheral | Settings | Use
DMA1 Stream 0 | Mem-to-peripheral; Request: SPI1 Transmit; Data Width: 8-bits; Priority: High | LCD Communication
NVIC1 | ADC1; ADC2; EXTI Line [9:5]; TIM1; TIM3; SPI1 | Interrupt Controller
ADC1 / ADC2 | Single Conversion Mode; Independent; 16-bit resolution; Regular Conversions | Read Joysticks
TIM1 | FreeRTOS Defaults (1000Hz Tick Rate) | FreeRTOS Clock
TIM3 | Prescaler: 149; Counter Period: 29999 | Timer to Begin ADC Conv
SPI 1 | Motorola; 8-bit data; CPOL: Low; CPHA: 1 Edge; Prescaler: 2 (25MBits/s); MSB First | LCD Communication
SPI 2 | Motorola; 8-bit data; CPOL: Low; CPHA: 1 Edge; Prescaler: 8 (6.25MBits/s); MSB First | Radio Communication
FREERTOS_M7 | Software pack for FreeRTOS | System OS

Table 13: Remote Control Peripheral Settings

DMA1 Stream 3 | Mem-to-peripheral; Request: TIM4_CH3; Data Width: Half-Word; Priority: High | ESC DShot Comm. M3
DMA1 Stream 4 | Mem-to-peripheral; Request: TIM3_CH4; Data Width: Half-Word; Priority: High | ESC DShot Comm. M4
DMA1 Stream 0 | Mem-to-peripheral; Request: UART5_RX; Data Width: 8-bits; Priority: Med; Circular FIFO | Rangefinder
DMA 2 Stream 0 | Mem-to-peripheral; Request: USART1_RX; Data Width: 8-bits; Priority: Med; Circular FIFO | 2D LiDAR
NVIC1 | EXTI Line [9:5]; DMA (all above) | Interrupt Controller
TIM1 | FreeRTOS Defaults (1000Hz Tick Rate) | FreeRTOS Clock
TIM3 | PWM Mode; Prescaler: 9; Counter Period: 24 | DShot Timer
TIM4 | PWM Mode; Prescaler: 9; Counter Period: 24 | DShot Timer
TIM7 | Prescaler: 14999; Counter Period: 65535 | Radio Recovery Timer
I2C 1 | Fast Mode (400KHz); 7-bit Address | Pressure Sensor
I2C 2 | Fast Mode (400KHz); 7-bit Address | IMU
SPI 2 | Motorola; 8-bit data; CPOL: Low; CPHA: 1 Edge; Prescaler: 8 (6.25MBits/s); MSB First | Radio
UART 5 | 115200 baud; 1 start bit; 8 data bits; 1 stop bit; 16x Oversample; RX and TX | Rangefinder
USART 1 | 230400 baud; 1 start bit; 8 data bits; 1 stop bit; 16x Oversample; RX Only | 2D LiDAR
FREERTOS_M7 | Software pack for FreeRTOS | System OS
Table 14: Drone Peripheral Settings

Grove 6-Axis IMU

The Grove 6-Axis IMU uses the BMI088, which is a 6-axis IMU (3-axis accelerometer and 3-axis

gyroscope) designed for arial vehicle applications. The module communicates with the drone’s MCU with

I2C running at 400KHz. In this project, the data is read from the IMU in polling mode, though the module

does have pins for interrupts. Further specifications of the IMU can be found in Figure 6, the product

wiki page [15], and the BMI088 datasheet [19].

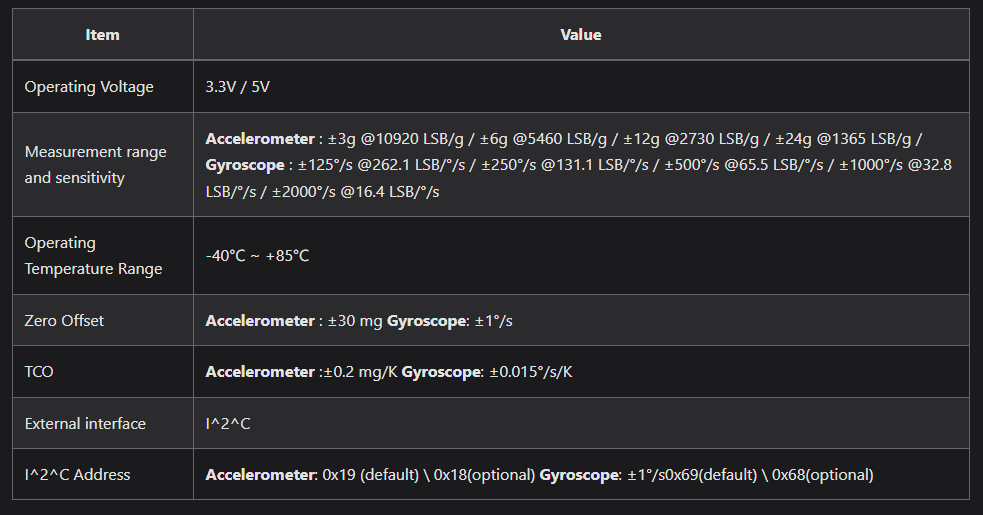
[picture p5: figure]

Figure 6: IMU Specifications Adapted from [15]

Table 15 contains the initialization values for both the accelerometer and gyroscope on the BMI088 IC.

These are not necessarily the only values that will work. For example, the gyroscope may not need a

measurement range of +/- 250 deg/s, and the accelerometer may not need a range of +/- 24g. Similarly,

the filtering of both sensors’ data should be adjusted based on the application; the values chosen in this

project are a balance between filtering to eliminate noise caused by vibrations and having a fast-enough

output data rate.

### BMI088 Initialization

Chip | Register | Address | Default Value | Value Needed | Description
ACC | ACC_PWR_CTRL | 0x7D | 0x00 | 0x04 | Power on
ACC | ACC_PWR_CONF | 0x7C | 0x03 | 0x00 | Set to active mode
ACC | ACC_CONF | 0x40 | 0xA8 | 0x8A | 4-fold oversample; 400Hz data rate
ACC | ACC_RANGE | 0x41 | 0x01 | 0x03 | +/- 24g range
GYRO | GYRO_LPM1 | 0x11 | 0x00 | 0x00 | Normal power mode
GYRO | GYRO_BANDWIDTH | 0x10 | 0x80 | 0x03 | 47Hz Filter BW
GYRO | GYRO_RANGE | 0x0F | 0x00 | 0x03 | +/- 250 deg/s range

Table 15: BMI088 Register Initialization Values

Ferimon ICP-10111

The Ferimon ICP-10111 pressure sensor communicates with the MCU using the I2C protocol at 400KHz.

Like the IMU, the data is received through polling. A data packet from the pressure sensor contains both

temperature and pressure measurements, however, they are not in a usable format. The temperature

data can be converted to Celsius, and the pressure data can be converted to Pascals through the

equations shown in Figure 7. For the pressure data conversion A, B, and C are values calculated in

software with functions provided by the chip manufacturer. More specifications on the ICP-10111 and

software functions to use the chip can be found in the datasheet [13].

Figure 7: Temperature and Pressure Conversion Equations Adapted from [13]

SpeedyBee F405 ESC

The SpeedyBee F405 ESC communicates with the MCU through the DShot600 protocol, which operates

at 600,000 bits per second. There is one wire connected to the MCU for each motor. The ESC accepts

values ranging from 0 – 2047; values from 0 – 47 are commands, while values from 48 – 2047 are

throttle values. On startup, the ESC needs to receive zero throttle for each of the motors before it will

start running. In this project, DMA is used to send DSHOT data packets to the ESC with one DMA channel

assigned to each motor. Four timers are used to measure the pulse widths of the packet transmission

since bit-values are determined by the pulse widths on the data transmit line. More details on the

SpeedyBee F405 ESC can be found in the datasheet [20].

NRF24L01+PA+LNA

The NRF24 radio is implemented on both the drone and the remote control. Since the NRF24 cannot

handle receiving and transmitting at the same time, acknowledgement packets are used to synchronize sending and receiving between the two systems. The drone’s radio is initialized as the primary

transmitter while the controller is the primary receiver. This means that the drone initiates all data

transactions by sending a packet. When the controller’s radio receives the packet, it will immediately

send an acknowledgement-payload back to the drone. This payload indicates to the drone that the

controller received the data, and it also contains joystick data from the controller. The datasheet for the

NRF24 [16] contains more information on the registers and functionality of the module.

Table 16 contains the initialization-values of the radio’s register for both the drone and controller. Not all

the values are needed to make the radios function; registers like data rate and channel frequency can be

changed, but they need to match on both the drone and controller. The only difference between the

radio initializations is that the drone is set as the transmitter while the controller is set as the receiver.

### NRF Initialization

Register | Address | Default Value | Value Needed | Description
CONFIG | 0x00 | 0x08 | 0x0A | Power on; TX mode (DRONE)
CONFIG | 0x00 | 0x08 | 0x0B | Power on; RX mode (CONTROLLER)
DYNPD | 0x1C | 0x00 | 0x01 | Enable dynamic payload for pipeline 0
EN_AA | 0x01 | 0x3F | 0x3F | Enable auto-ack
FEATURE | 0x1D | 0x00 | 0x06 | Enable dynamic payload and ack-payload
RF_SETUP | 0x06 | 0x0E | 0x0E | 2Mbps data rate; 0dBm
RF_CH | 0x06 | 0x02 | 0x64 | 2500MHz channel frequency
SETUP_RETR | 0x04 | 0x03 | 0xFF | 4ms delay b/w re-TX; Re-TX 15 times

Table 16: NRF24 Initialization for Drone and Controller

HiLetgo ILI9341 2.8” LCD

The LCD is part of the controller and is communicated to through SPI. The SPI transmit and receive are

handled through DMA on the MCU. Although the LCD has touch-screen capabilities, these are not

utilized in this project. Table 17 shows the command sequence to initialize the LCD in this project. These

commands are from the ili9341_initialize(ili9341_t *lcd) function, which is part of the LCD library [9]

used in this project. The commands in the table are sent to the LCD from top to bottom. The ILI9341 IC

datasheet [18] contains more information on the registers and how to use the LCD.

### ILI9341 Initialization Sequence

Command | Command Data | Purpose
0x01 | None | SW RST
0xCB | 0x39, 0x2C, 0x00, 0x34, 0x02 | Power Control A
0xCF | 0x00, 0xC1, 0x30 | Power Control B
0xE8 | 0x85, 0x00, 0x78 | Driver Timing Control A
0xEA | 0x00, 0x00 | Driver Timing Control B
0xED | 0x64, 0x03, 0x12, 0x81 | Power On Sequence Control
0xF7 | 0x20 | Pump Ratio Control
0xC0 | 0x23 | Power Control VRH [5:0]
0xC1 | 0x10 | Power Control SAP[2:0], BT[3:0]
0xC5 | 0x3E, 0x28 | VCM Control
0xC7 | 0x86 | VCM Control 2
0x36 | 0x48 | Memory Access Control
0x3A | 0x55 | Pixel Format
0xB1 | 0x00, 0x18 | Set Frame Radio Control to Standard RGB
0xB6 | 0x08, 0x82, 0x27 | Display Function Control
0xF2 | 0x00 | 3Gamma Function Disable
0x26 | 0x01 | Gamma Curve Select
0xE0 | 0x0F, 0x31, 0x2B, 0x0C, 0x0E, 0x08, 0x4E, 0xF1, 0x37, 0x07, 0x10, 0x03, 0x0E, 0x09, 0x00 | Positive Gamma Correction
0xE1 | 0x00, 0x0E, 0x14, 0x03, 0x11, 0x07, 0x31, 0xC1, 0x48, 0x08, 0x0F, 0x0C, 0x31, 0x36, 0x0F | Negative Gamma Correction
0x11 | None | Exit Sleep
0x29 | None | Turn Display On
0x36 | 0x28 | Set Screen Orientation to Left

Table 17: Init Sequence for LCD from ili9341.c in [9]

FHL-LD19 LiDAR

The 2D LiDAR is extremely simple to set up since it does not have an RX pin. Once the LiDAR is powered,

it will begin transmitting packets through UART at 230400 baud. One UART transmission contains a start

bit, eight data bits, and a stop bit. Since there is no way to synchronize the MCU’s data reception with

the LiDAR, the LiDAR’s ground is connected to a TIP120 transistor. The base of the transistor is connected

to a pin on the MCU which allows the MCU to turn on/off the LiDAR. This allows the MCU to boot and

initialize everything before powering-on the LiDAR, so it does not become desynched from the start of the LiDAR data reception. Additionally, to make sure that the data reception is not desynched after boot-

up, the data is received through DMA so that the CPU does not need to switch from other processes just

to receive the LiDAR data.

The LD19 has a PWM pin which is used to control the rotation of the LiDAR’s motor. If the PWM pin is

connected to ground, as it is in this project, the motor rotates ten times per second. Since the LiDAR

measures at 4500Hz and rotates at 10Hz, it measures about 450 times per second, which results in a 0.8-

degree resolution. This means that there is a difference of about 0.8-degrees between any two LiDAR

distance measurements. More information on the LD19 can be found on the manufacturer’s wiki page

[3].

2212 920KV BLDC Motors

Four BLDC motors are needed for this project. Each motor is connected to the ESC which drives each of

them individually. It is important to note that on a quadcopter, the motors diagonal from each other on

the frame must spin in the same directions. That is to say, the front left and back right motors should

spin the same direction, but opposite the direction of the front right and back left motors. This approach

is used to balance the net torque from the motors’ rotations. If not implemented correctly, the torques

from the motors will cause the drone to rotate on its z-axis (yaw).

Joysticks

The controller has two joysticks for controlling the drone: a left joystick for throttle and yaw, and a right

joystick for pitch and roll. Although not essential to the project, the left joystick’s y-axis (throttle) is not

connected to a spring, so it will not automatically center itself. The yaw, pitch, and roll axis will

automatically center themselves. Each axis on the joysticks is connected to an ADC channel on the MCU.

The ADCs periodically read the values of the joysticks which are translated into control signals for the

drone in software. How often the joystick values are sampled is not very important. Currently they are being sampled every 30ms, which is fast enough that control of the drone feels responsive, but also not

so fast that the other controller tasks are being interrupted constantly.

### Software

All the code for this project is written in C. Since the project uses an STM32 MCU, STM32CubeIDE 1.12.1

is used to program and debug the drone and controller. Both the drone and controller use FreeRTOS to

handle the various tasks on each device. Aside from the Blink tasks, each task has a UML diagram

associated with it. These UML diagrams contain brief descriptions of the tasks, essential variables each

task uses, and essential functions each task uses.

Remote Control

Figure 8 illustrates the software block diagram for the controller. There are only two tasks running on the

controller, the LCD Display Task, and the Blink Task; everything else is handled through interrupt service

routines (ISRs).

Figure 8: Controller Software Diagram

Blink Task

The Blink task toggles an LED on the NUCLEO board every second. The purpose of this task is to give

visual confirmation that the system tasks are running, and that no major errors have occurred. Code for

the Blink task is shown in Figure 9.

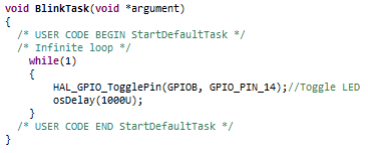
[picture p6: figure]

Figure 9: Blink Task Code

ADC Conversion Complete ISR

The ADC Conversion Complete ISR runs every time the MCU’s ADCs finish reading the positions of the

joysticks. This task first processes the joystick readings and then stores them in an array which is sent to

the drone via the radio. Before getting stored in the radio buffer, the raw joystick readings are processed

in a moving-average filter to eliminate some high-frequency noise and then scaled to range from 0 –

2047. The scaling is primarily due to the DSHOT protocol on the ESC requiring throttle values between 0

– 2047. Although this means only the throttle readings need to be scaled, all the values are scaled to

keep them consistent. Code for this ISR is shown in Figure 37 in the appendix.

Figure 10 illustrates a UML diagram for the ADC Conversion Complete ISR. The sums_index variable and

signed integer arrays are all used for the moving average filter, which averages the last five joystick

readings for throttle, yaw, pitch, and roll. The adc_val variables temporarily stores the most recent ADC

conversion before it is processed and stored in the RadioTX array.

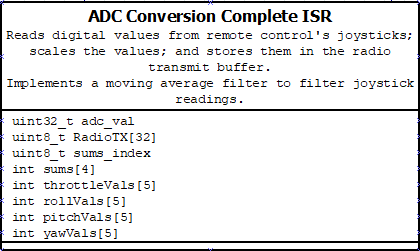
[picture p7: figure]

Figure 10: ADC Conv. Complete ISR UML

LCD Display Task

The LCD Display Task receives the 2D LiDAR data from the drone via the radio. Once it has the data, this

task parses it into packets and transmits the data to the LCD to display any detected obstacles around

the drone. The LCD display task will update the display for every LiDAR packet it receives. These LiDAR

packets contain a start angle, end angle, and twelve distance measurements taken between the start and

end angles. The display task will use this data to first clear any drawn pixels in the same direction as the

new distance data and then draw new pixels to represent the distances to the most recently measured

objects.

Figure 11 shows the UML for the LCD Display task. The integer array, packet, contains LiDAR data from

the quadcopter. The beginAngle and endAngle variables contain the start and end angles of the LiDAR

measurements and are passed into the displayData function along with the LiDAR data packet. The

diaplayData function handles updating the LCD with the most recent LiDAR measurements. The ili9341_t

struct, ili9341_fill_rect, and ili9341_fill_screen are part of a C library for the ILI9341 LCD driver [9]. Code

for the LCD Display task is shown in Figure 12.

Figure 11: LCD Display Task UML

Figure 12: LCD Task Code

Radio RX/TX ISR

The Radio RX/TX ISR is triggered whenever the controller’s radio receives a packet from the drone. Once

a packet containing 2D LiDAR data is received, this task sends the data to the LCD Display task and then

transmits and acknowledgement packet, containing the joystick data, to the drone.

Figure 13 is the UML for the Radio RX/TX ISR. RadioRX and RadioTX are integer buffers for receiving and

transmitting data through the radio. The radioCount variable is used to count the number of radio

transmissions. An LED on the controller is toggled every 300 transmissions. The status variable is used to

check the status of the NRF24L01P which indicates events and errors. The nrf24l01p_write_ack_payload

is used to write to the radio’s acknowledgement payload which is sent back to the quadcopter along with

an acknowledgement signal after each successful reception. Lastly, the nrf24l01p_rx_receive is a library

function from [12] and is used to receive data transmitted by the quadcopter. Code for the radio ISR is

shown in Figure 14, while Figure 15 illustrates code for nrf24l01p_write_ack_payload.

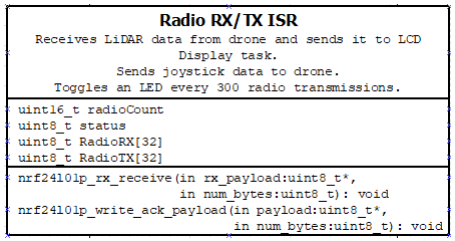
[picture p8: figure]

Figure 13: Radio RX/TX ISR UML

Figure 14: Controller Radio ISR Code

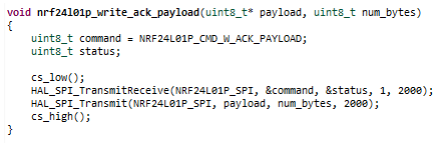
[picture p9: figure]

Figure 15: Radio Write Ack Payload Function

Quadcopter

Figure 16 illustrates the software block diagram for the drone. The drone has eight tasks and one ISR.

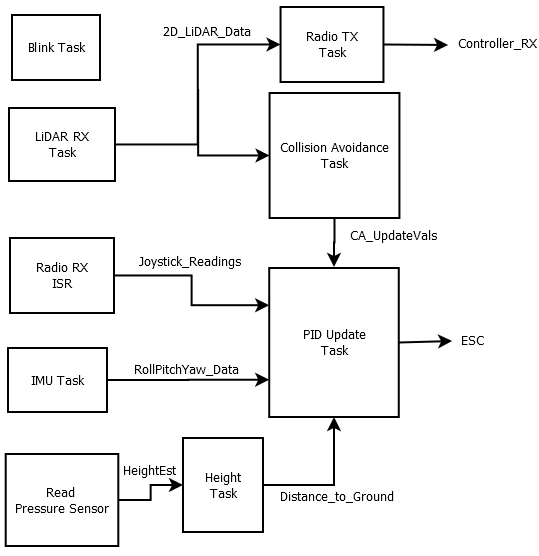
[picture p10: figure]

Figure 16: Drone Software Diagram

Blink Task

The drone’s Blink task functions exactly like the one in the controller. It simply toggles an onboard LED to

indicate that no major errors have occurred.

LiDAR RX Task

The LiDAR RX task receives and analyzes data from the 2D LiDAR. The raw LiDAR data consists of forty-

seven bytes containing distance measurements (twelve per packet), angle measurements, rotation rates,

light intensity, a CRC, packet header, and packet version. The only data needed from the packet are the

distance measurements, angle measurements, and CRC. When raw data is first received, the LiDAR RX task checks to make sure the data is valid by sending it through a CRC function. If the data turns out to

be invalid, it is discarded. Otherwise, it is passed into a parsing function to get an array containing only

the angle data and distance measurements. The parsed data is then sent to the radio transmitter, and

the Collision Avoidance task. Code for the CRC function and parsing function is shown in Figure 36 and

Figure 35, respectively. Both figures are in the appendix.

Figure 17 is the UML diagram for the LiDAR RX task. The array, packet, stores the raw LiDAR data that is

transferred to the task through DMA. The CalCRC8 function calculates the CRC for the received data

packet. Only if the LiDAR data is valid does the getLiDARMeasurements function process the LiDAR data

into two packets, one containing the data that is sent over the radio to the controller, and another

containing data used in the obstacleDetection function. The reason for having two packets is that the

data sent over the radio is compressed to make the radio transmissions faster, while the full LiDAR data

packet is used for obstacle detection. Figure 18 contains the code for getLiDARMeasurements. The

obstacleDetection function performs the first step of the collision avoidance algorithm by updating an

array containing all measured distances around the quadcopter and determining the closest obstacles in

each sector; this process is explained further in the ‘Collision Avoidance Task’ section. Figure 42 contains

code for the obstacleDetection function.

Figure 17: 2D LiDAR Task UML

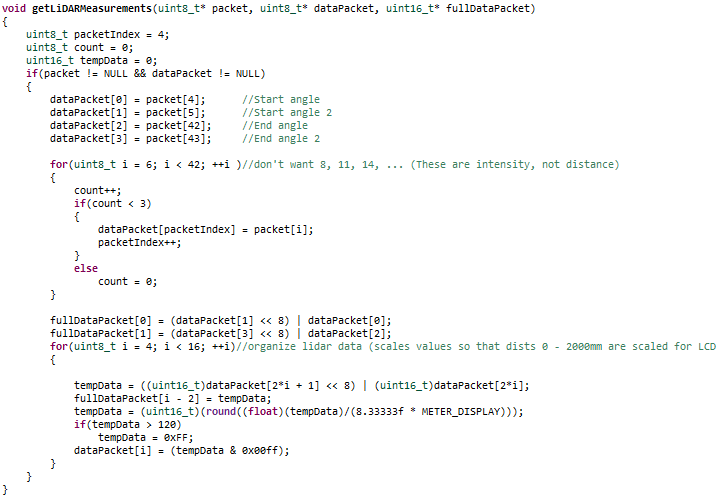
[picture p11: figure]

Figure 18: LiDAR Get Measurements Function

Radio RX ISR

The Radio RX ISR handles the reception of acknowledgement packets from the controller, which contain

joystick data. When a packet is received, it is parsed for the joystick readings, which are then sent to the

PID Update task through a queue.

Figure 19 shows the UML diagram for the Radio RX ISR. The nrf24l01p functions are from a C library [12]

and handle event flags and the data reception from the controller. Like in the controller, the RadioRX

array is a buffer for storing received data, while the status variable stores data read from the radio’s

status register. The motor_vals variable is a struct storing four 16-bit integers; the name does not make

sense in this context, but the joystick values are later used in calculations for the motors’ throttle values.

Code for this ISR is shown in Figure 40.

Figure 19: Radio RX ISR

Radio TX Task

The Radio TX Task runs every few milliseconds and transmits whatever LiDAR data is stored in its buffer

over to the controller. Figure 20 shows the UML for this task. The nrf24l01p_tx_trasnmit function is also

from the C library for the NRF24L01P [12], and handles transmitting the data in the RadioTX buffer. The

code for this task is shown in Figure 21.

Figure 20: Radio TX Task UML

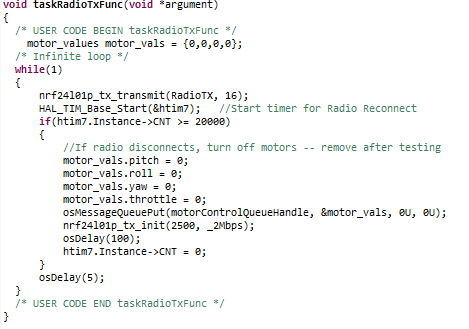
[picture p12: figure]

Figure 21: Drone Radio TX Task Code

Collision Avoidance Task

The Collision Avoidance task implements two of the three stages in the collision avoidance algorithm. As

mentioned previously, the three stages are obstacle detection, hazard assessment, and obstacle

avoidance. The obstacle detection step is performed in the LiDAR RX task, while hazard assessment and

obstacle avoidance are performed in the Collision Avoidance task.

In this algorithm, the area around the drone is divided into sectors and each sector is assigned one PID

controller that controls the distance between the drone and the closest obstacle its sector. The setpoint

for each controller is the minimum distance obstacles can be from the drone before it tries to avoid

them, while the current distance (the PID measurement) is the distance measured by the 2D LiDAR.

A diagram illustrating the features of the collision avoidance algorithm is shown in Figure 22. In this

diagram, the area around the drone is divided into eight sectors. The hazard assessment stage

determines which of the obstacles the drone is most likely to collide with based on the drone’s distance

to the obstacles, while the obstacle avoidance stage calculates update values for the drone’s motors

using motor-mixing equations.

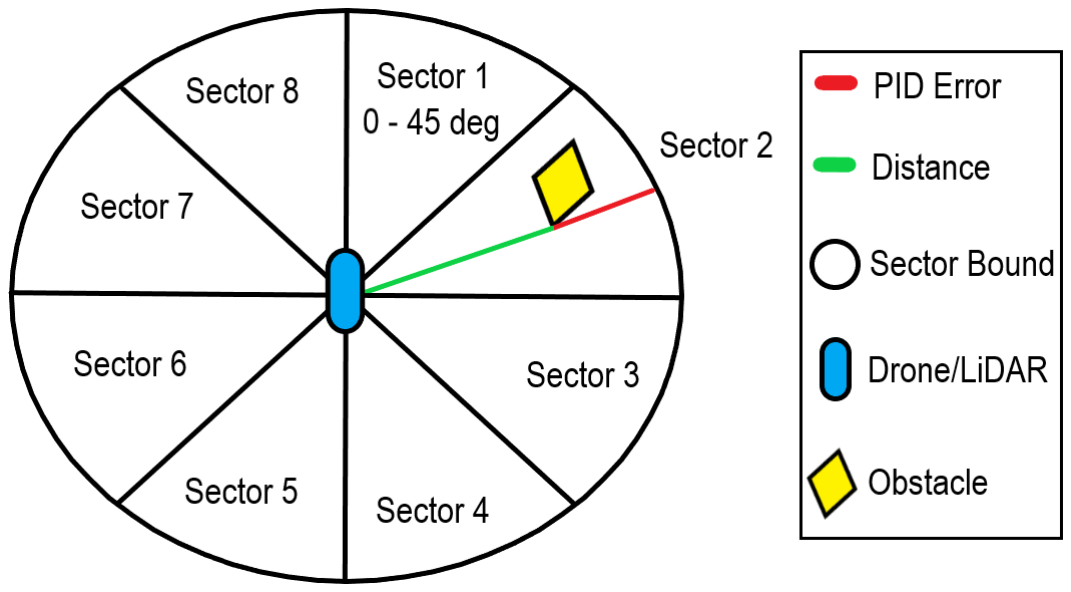
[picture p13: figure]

Figure 23 is the Collision Avoidance task UML diagram. The initCA function initializes the algorithm’s

distance-measurement buffer, which contains all measured points around the drone. It also initializes the

PID controllers for each sector (sectorControllers[8]), and structures containing the closest obstacle in

each sector. The closest obstacle for each sector is recorded as a polar-coordinate pair. The

obstacleAvoidance function calculates update values for each sector by sending the closest distance in

each sector into PID update functions and storing the output in the sectorAdjustments array. The values

in this array are summed together to find the final adjustments for each of the four BLDC motors. Code

for initCA is shown in Figure 42, and code for obstacleAvoidance is shown in Figure 43.

Figure 22: Collision Avoidance Algorithm Diagram

Figure 23: Collision Avoidance Task UML

Figure 24 shows the code for the Collision Avoidance task. After obstacleAvoidance is called, the task

creates update values for the four motors through motor-mixing equations. These equations add

portions of the updates from each of the PID controllers to the motor throttles. Motors that are closer to

a sector get a larger portion of the update-values for that sector. Like the flight controller throttle

updates, complimentary motors are updated with values that are the same magnitude, but opposite

signs. For example, if there is an obstacle in the first sector, motor three would get the largest update

value added to its throttle since it is the closest motor, while motor two, the one furthest away, gets that

same update value subtracted from its throttle.

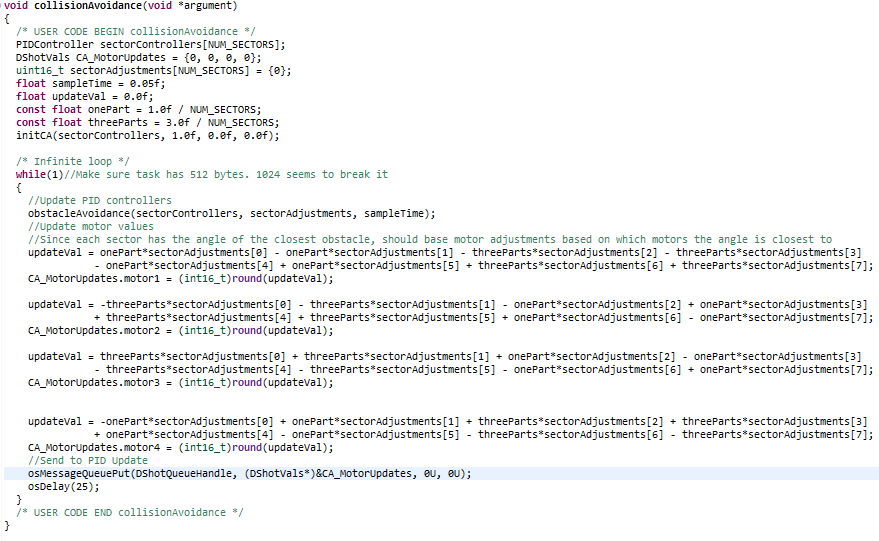
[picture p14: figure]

Figure 24: Collision Avoidance Task Code

Read IMU Task

The Read IMU task handles sending commands and receiving data from the BMI088 IMU. Once the data

is collected, it is filtered and then sent to the PID Update task to be used in the PID control equations.

The raw IMU data goes through two filters, an FIR filter and an extended Kalman filter. The FIR filter is a

low-pass filter that eliminates some of the high-frequency noise from the data. The Kalman filter is used

to estimate the current roll and pitch angle of the IMU using the rotation rates from the gyroscope and

the linear acceleration from the accelerometer. Once the data is done being processed by the Kalman

filter, the roll angle, pitch angle, and yaw rotation rate are sent to the PID Update task. The IMU task

code is shown in Figure 39 in the appendix.

Figure 25 is the UML diagram for the Read IMU task. The bmi08 functions are from a C library for the

BMI088 [10]. These functions are for reading and writing to the BMI088’s registers, including the data registers for the accelerometer and gyroscope data. FIRFilter_Init, FIRFilter_Update, and the FIRFilter

struct are all used in the low-pass FIR filter which is used to filter the raw IMU data before sending it into

the extended Kalman filter. The KalmanFilterRollPitch struct stores variables needed for the extended

Kalman filter, including the predicted roll and pitch angles. EKF_Predict and EKF_Update perform the

core operations of the extended Kalman filter and output the estimated roll and pitch angles of the

quadcopter. These values, along with the yaw rotation rate, are stored in the rotationVals struct (which is

just three floats) and sent to the PID Update task. The FIR filter code is from [8], while the extended

Kalman filter code is adapted from [7] and [14].

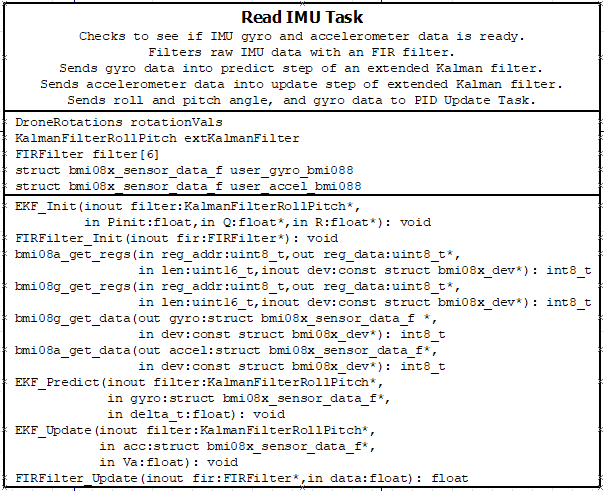
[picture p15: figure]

Figure 25: Read IMU Task

Read Pressure Sensor Task

The Read Pressure Sensor task reads pressure data from the drone’s pressure sensor and converts the

data into height estimations. The estimated height is sent to the Height task through a queue. Figure 26

shows the UML for this task. The inv_invpres_process_data function is from the ICP-10111 datasheet

[13], and uses the data read from the pressure sensor to estimate the atmospheric pressure and height,

which are stored in the pressure and height float variables. The estimated height is stored in meters.

Figure 27 shows the code for the Read Pressure Sensor task.

Figure 26: Read Pressure Sensor Task

Figure 27: Read Pressure Sensor Task Code

Height Task

The Height task receives height estimates from the Read Pressure Sensor task and the LiDAR rangefinder,

and then combines the measurements to calculate an estimate for the drone’s distance from the ground.

The first ten measurements of the rangefinder are used to zero the pressure sensors height readings so

that the pressure sensor readings are relative to the drone’s starting height rather than sea level. The

height estimate favors the rangefinder within six meters of the ground but begins to favor the pressure

sensor until 12 meters, where the rangefinder is ignored entirely. The estimated height of the drone is

sent to the PID Update task, though it is not used for anything yet.

Figure 28 illustrates the Height task UML diagram. The ‘RF’ functions are used to initialize the

rangefinder so that it measures every 200ms. The rangefinderBuffer contains the raw data read from the

rangefinder; this data is used to calculate the measured distance in meters, which is then stored in

rangeFinderHeight. The altimeterHeight variable contains the pressure sensor height estimate received

from the Read Pressure Sensor task. Code for the rangefinder functions are illustrated in Figure 41 and

code for the task itself is shown in Figure 44; both figures are in the appendix.

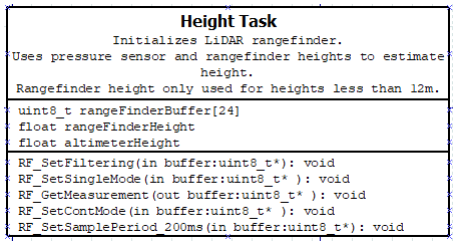
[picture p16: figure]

Figure 28: Height Task UML

PID Update Task

The PID Update task receives data from the other tasks and uses that data to adjust the throttle values of

each BLDC motor. The IMU and joystick data are used in PID control equations to control the flight and

balance of the drone; the data from the Collision Avoidance task is used along with the IMU data to

determine if the drone is going to collide with an obstacle; and the height of the drone may eventually

be used for hovering and avoiding collisions with the ground. Once all the data is received and motor

update values are calculated, the PID Update task sends four DSHOT signals to the ESC which then drives

the four motors to adjust the movement of the drone.

The drone’s flight controller consists of three PID controllers, one for the roll angle, another for the pitch

angle, and the third for yaw rotation rate. The PID controllers take in the IMU data as the drone’s current

state and control to setpoints calculated from the joystick control values. Code for the PID controllers is

shown in Figure 38 in the appendix; these equations are adapted from [5].

Figure 29 shows the UML diagram for the PID Update task. The PIDController structs are used to store

the gain-values of each controller along with the previous measurement, previous error, and other terms

used in the PID_Update function. PID_Update calculates adjustments to the four BLDC motors using a

setpoint (joystick data) and a measurement (IMU data). These adjustments are stored in the update

variables for roll, pitch, and yaw, which are later summed with the base throttle taken directly from the

throttle joystick value. The final throttle values are written to the ESC through the dshot_write function,

which is from a DSHOT protocol C library [11].

Figure 29: PID Update Task UML

## Encountered Problems

One problem encountered throughout this project was difficulty communicating with the IMU, which

caused multiple tasks to be delayed by a couple of weeks. This problem was solved by switching from SPI

communication to I2C. Another issue was that the vibrations from the quadcopter’s motors caused too

much noise in the IMU accelerometer readings. This problem was resolved after adjusting the

parameters of the IMU’s built-in low-pass filter. The IMU data rate is slower, but it blocks out much more

high-frequency noise. A third issue was that the 2D LiDAR would toggle on and off during operation. The

issue seems to have been lack of power since it stopped after moving the LiDAR to its own buck

converter.

The most significant problem encountered throughout this project was the instability of the drone’s

flight controller observed during test flights and PID tuning. At high-enough throttle values (200+), the

quadcopter oscillates on the x and y-axis. These oscillations grow until the quadcopter nearly flips upside

down. This issue occurs even when the PID controllers are turned off, which indicates it may be an issue

with the motors or the design of the drone frame. This problem has not been solved even after redesigning and rebuilding the drone frame, debugging the IMU and flight-control software, and

implementing angular rate PID controllers instead of angle controllers (also tried angular rate and angle

controllers combined). Regardless of what was changed, the oscillations seemed to remain the same.

## Assembled Project

Figure 30 shows the assembled quadcopter drone. Overall, the drone weighs approximately three

pounds. All the components are wired together inside the central compartment and the wires

connecting the motors to the ESC run through the drone’s hollow limbs. Although not visible in the

picture, the rangefinder is mounted on the underside of the drone, pointing downwards.

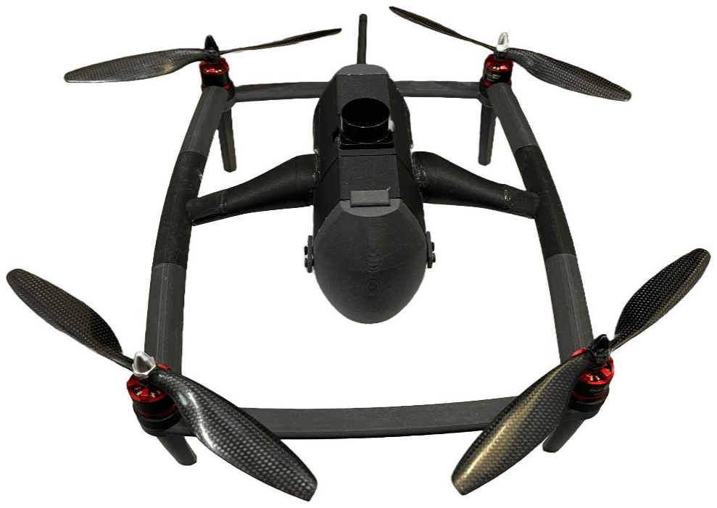
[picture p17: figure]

Figure 30: Assembled Quadcopter Drone

Figure 31 and Figure 32 show the assembled controller. Like the quadcopter, all the components are

wired together on the inside. The face of the controller shows the LCD, joysticks, a power switch, and

two LEDs (red for power, green for radio connection). The front of the controller has a hole for the

controller’s battery and antenna.

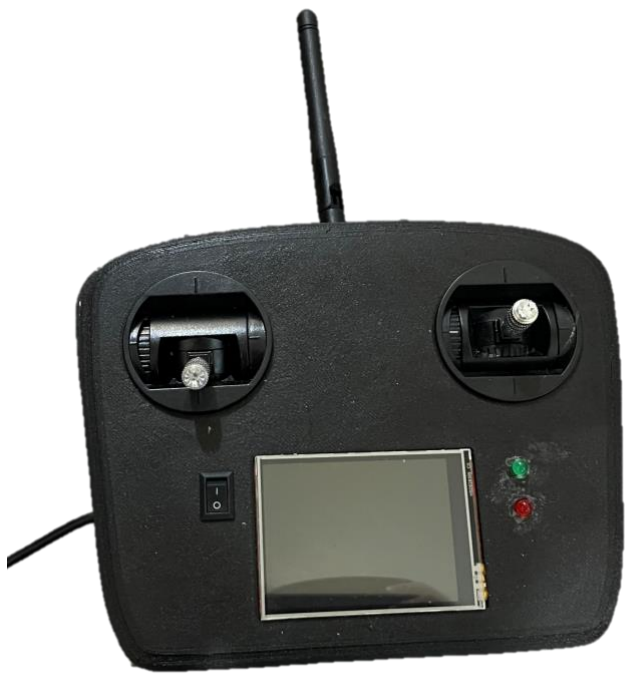
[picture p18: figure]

Figure 31: Assembled Controller - Top-Down

Figure 32: Assembled Controller – Front

## Testing

To prove that the project met the proposed requirements, a series of tests were performed to test the

related functions of the drone and controller. Many of the requirements had overlap in their

functionality. For most requirements, videos were used as proof. Requirements 11, 15, and 16 were

stretch goals, and were not implemented. Table 18 shows the requirement, test method, and results

from the tests performed. Overall, nearly every requirement was successfully tested and proven through

data, images, or videos. The only requirement test that did not completely pass was requirement five,

because the radio communication between the drone and controller was heavily delayed when the

controller was powered by battery.

Req.
Description | Test methodology | Results / Notes
1 | Drone has 4 propellers and
BLDC motors used for flight. Drone is custom-built for the project. | Images of the drone will be used to show that it is built from custom parts, and that it has four motors and propellers. | Test Passed. Included images of constructed drone as proof.
2 | Remote control is custom- built and used to operate the drone from a distance.

Use the controller to change the throttle, yaw, pitch, and roll controls on the drone.

Test Passed. Used images and videos from requirement seven as proof since they overlap.
3 Drone and controller have separate microcontrollers. The MCUs are fast-enough to process necessary data and respond in near real-time.

The MCUs can be verified by looking at the internals of the drone and controller. The
display speed on the
controller, and the drone's responsiveness to joystick controls and collision
avoidance can be used to
verify that the MCUs are fast-enough. Images/Videos will be used as proof.

Test Passed. All videos and images were taken with everything running on both the drone and controller. They showcase the PID controllers, joystick reading, IMU data, collision avoidance, LiDAR data display, and radio
communication.

4 The drone and controller communicate over radio at least 25 feet away.

Transmit data between the
drone and controller while they are at least 25 feet away and check if the data

Test Passed. A video was taken of the controller operating the drone at about 35 feet.

received on each end is
correct.
5 The drone and controller can be powered by rechargeable batteries.

Power-on and operate the
drone while both the drone and controller are powered by battery. Images/Videos
will be used as proof.

Test partially passed. For some reason radio communication runs very slowly when the controller is powered by battery.

6 The controller has an LCD screen that displays obstacles around the drone and updates at least 15 times a second.

Place obstacles around the drone and verify that the LCD updates to correctly show
the new objects. The refresh rate of the LCD will be tested by timing how often the LCD task runs (# times ran / time) and comparing the measured value with the required
value.

Test Passed. Timer and counter in LCD task were used to measure the LCD update rate. The CSV file has all data sent to serial monitor and the average refresh rate. The average was over 15 updates per second. Video shows LiDAR data display.

7 The controller has two joysticks read by the MCU's ADCs: one for throttle and yaw, and one for pitch and roll.

Each joystick will be tested individually to control the drone to prove that one
controls throttle and yaw, and the other controls pitch and roll.

Test Passed. Included image of constructed controller and videos for each test.

8 The drone uses a rotating LiDAR to detect obstacles. The LiDAR is active while drone is in flight. The LiDAR can detect obstacles three meters away.

Show that the rotating LiDAR data is being used to
determine the location of
obstacles. Verify that the LiDAR continues to run when the drone motors are active. Set obstacles three meters away from the drone and
verify that it can detect them.

Test Passed. One video
demonstrates the motor updates from the collision avoidance algorithm for obstacles around the drone. Another video
demonstrates that the drone can detect obstacles over three meters away. The rotating LiDAR is visible in both videos.
9 The drone's flight controller uses a 3-axis gyro and 3-axis accelerometer IMU to calculate adjustments to the motors' throttles.

Record and display data from the IMU and verify that the drone's PID controllers use that data to balance the
drone.

Test Passed. Added images of code for EKF using IMU data and PID controllers. Videos are of pure rate controller. Serial data is from angle controller.

10 The drone attempts to avoid obstacles it senses it will collide with.

Place obstacles around the drone and verify that the
motor adjustments
calculated by the collision avoidance (CA) algorithm will move the drone away from
the objects.

Test Passed. Video demonstrates the motor adjustments from the collision avoidance algorithm. The motors closest to the obstacle speed up when it gets too close (this would tilt the drone away from the object). The image shows serial data with the PID updates, setpoints, CA motor updates,

## Conclusion

Overall, the project was fairly successful. Despite the continued issues with the destabilization of the

drone’s flight controller, most of the requirements were implemented and successfully tested. As a

research project, this project was especially successful, since a lot was learned about designing and current angle, and angular rate of the drone.
12 The drone is controlled through the controller, but automatically attempts to avoid obstacles. (Semi-autonomous mode)

Show that the collision-avoidance algorithm outputs motor adjustments to avoid obstacles while the user is controlling the drone through the controller.

Test Passed. Video demos CA motor adjustments to avoid obstacles while the drone is being controlled through the controller. The collision avoidance speeds up the motors closest to the object, which are normally stopped because the controller is telling the drone to pitch forward. The images show serial data for collision avoidance with a front obstacle while the drone is being told to pitch and roll.
13 Drone estimates its distance from the ground with a range finder.

Use the rangefinder to
measure the drone's height at known distances and verify that the measurements are
correct.

Test Passed. Included images of setup and data. Raw data was averaged. Needed multiple trials to adjust pressure sensor offset

14 Drone estimates its distance from the ground with a pressure sensor. Pressure sensor and rangefinder data may be combined into a single height estimate.

Use the pressure sensor to measure the drone's height at known distances and verify that the measurements are
correct.

Test Passed. Tested alongside rangefinder (requirement 13). Rangefinder tended to
overestimate height, while pressure sensor tended to
underestimate it. The combined measurements became more
accurate due to this.
17 Most of the drone and controller housings are 3D printed.

The drone and controller
housing can be verified
visually. Images/videos of printing and the 3D models will be included as proof. STL files for the parts will be included too.

Test Passed. Included STL files for drone and controller. Included images of the 3D models. Included image and video of drone leg printing.

Table 18: Requirement Testing Data building quadcopters, developing collision avoidance algorithms, and using a 2D LiDAR. If this project

were to be done again, more time would be spent in the early stages of development to create a model

for the drone that can be controlled by the PID controllers. This would have potentially made tuning the

PID controllers much easier since more would be known about the system and more efficient methods

could be used to determine the PID gains.

## Glossary

IMU – Acronym for inertial measurement unit. This module is capable of sensing rotational and linear

accelerations.

GPS – Acronym for Global Positioning System. This module receives data from GPS satellites and uses

this data to calculate its position in relation to the surface of the planet using trilateration.

LiDAR – Acronym for Light Detection and Ranging. LiDAR modules send out pulses of light that reflect off

surfaces in the surrounding environment and return to the module. The LiDAR module uses time-of-

flight or triangulation to calculate how far away the obstacle is from the module.

PID – Acronym for proportional, integral, derivative. This term is generally associated with PID controllers

which are equations that use measurements and some kind of control system to reach a certain set of

parameters (i.e., reading a thermometer and using a heater to make a room reach a certain

temperature).

## Appendix

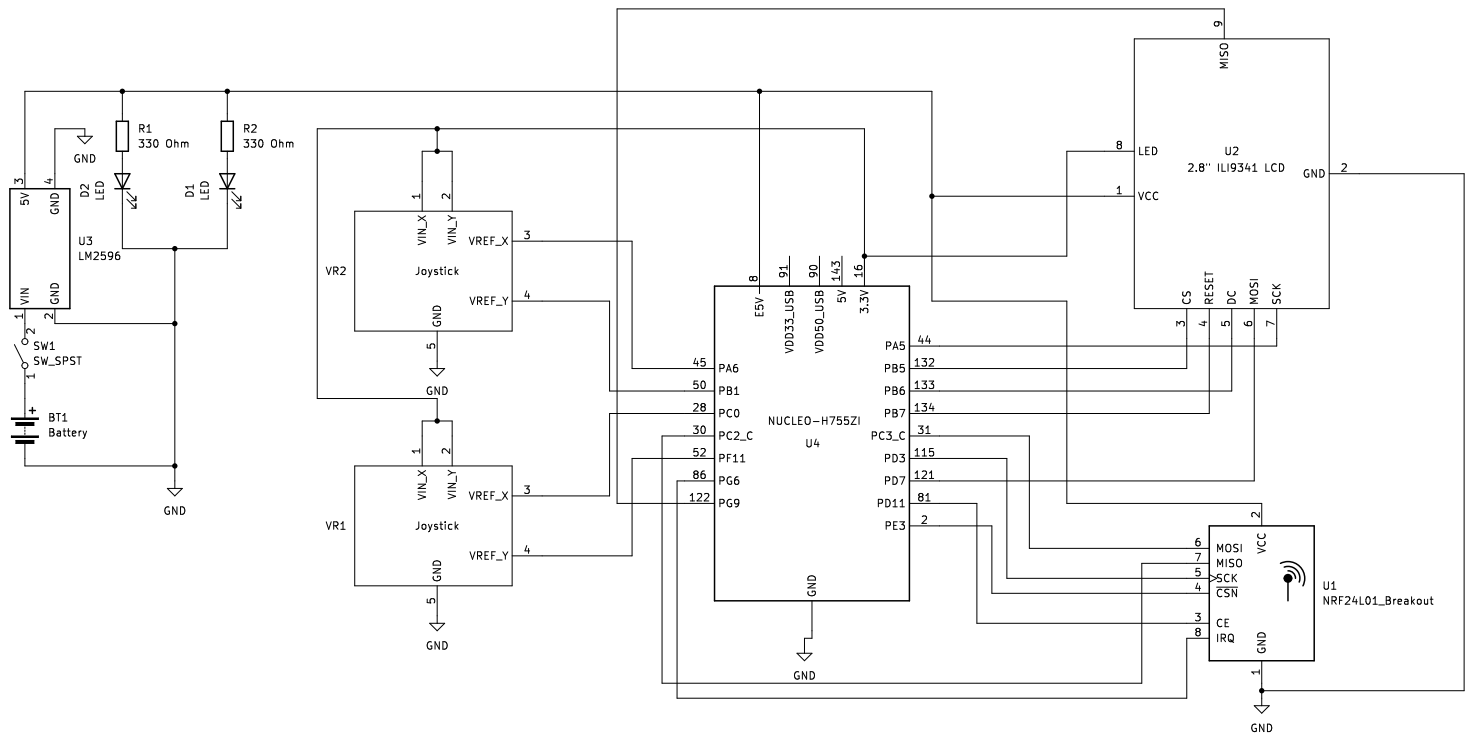
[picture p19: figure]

Figure 33: Controller Wiring Schematic

Figure 34: Drone Wiring Schematic

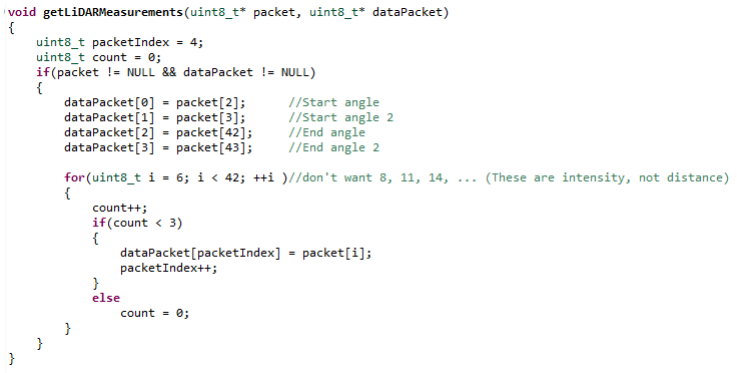
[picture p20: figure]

Figure 35: LiDAR Data Parsing Function

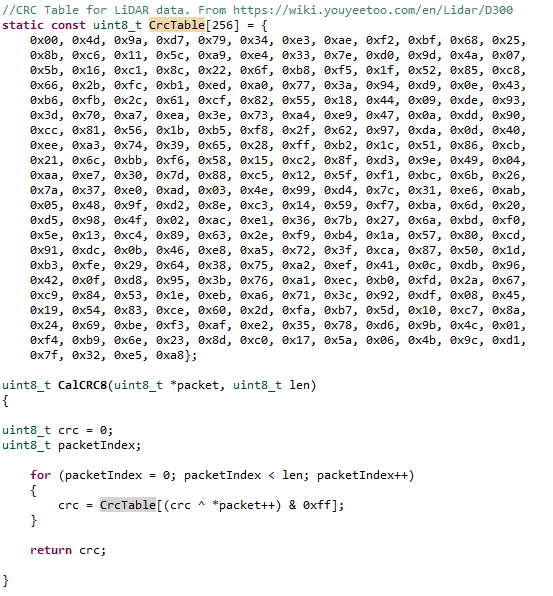
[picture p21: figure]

Figure 36: LiDAR CRC Function

Figure 37: ADC Conversion Complete ISR

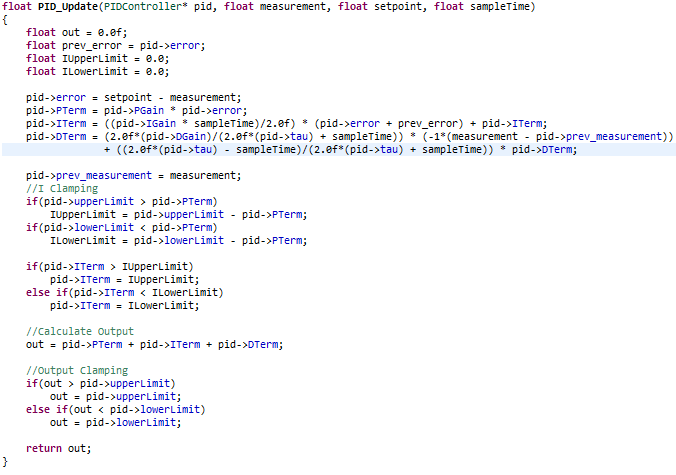
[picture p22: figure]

Figure 38: PID Control Equations. Adapted from [5]

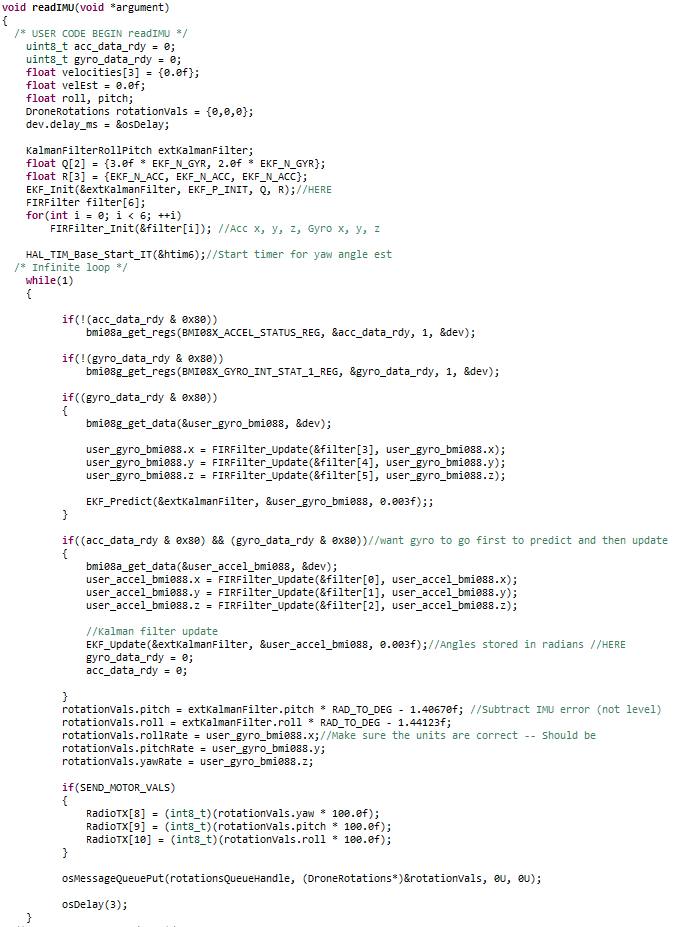
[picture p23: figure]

Figure 39: IMU Task

Figure 40: Drone Radio RX ISR

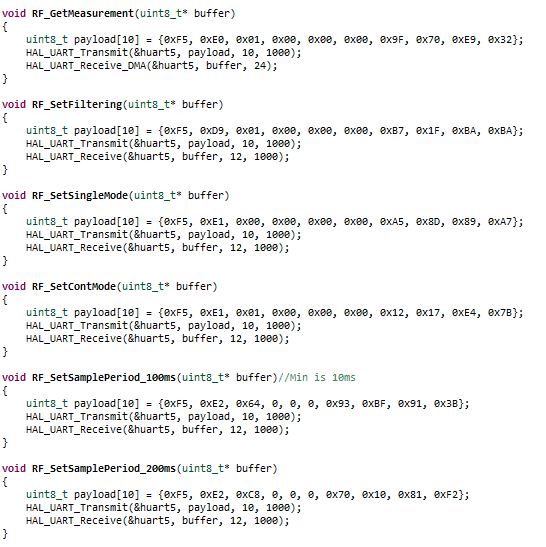
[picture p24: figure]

Figure 41: Rangefinder Functions

Figure 42: Init CA and Obstacle Detection Functions

Figure 43: Obstacle Avoidance Function

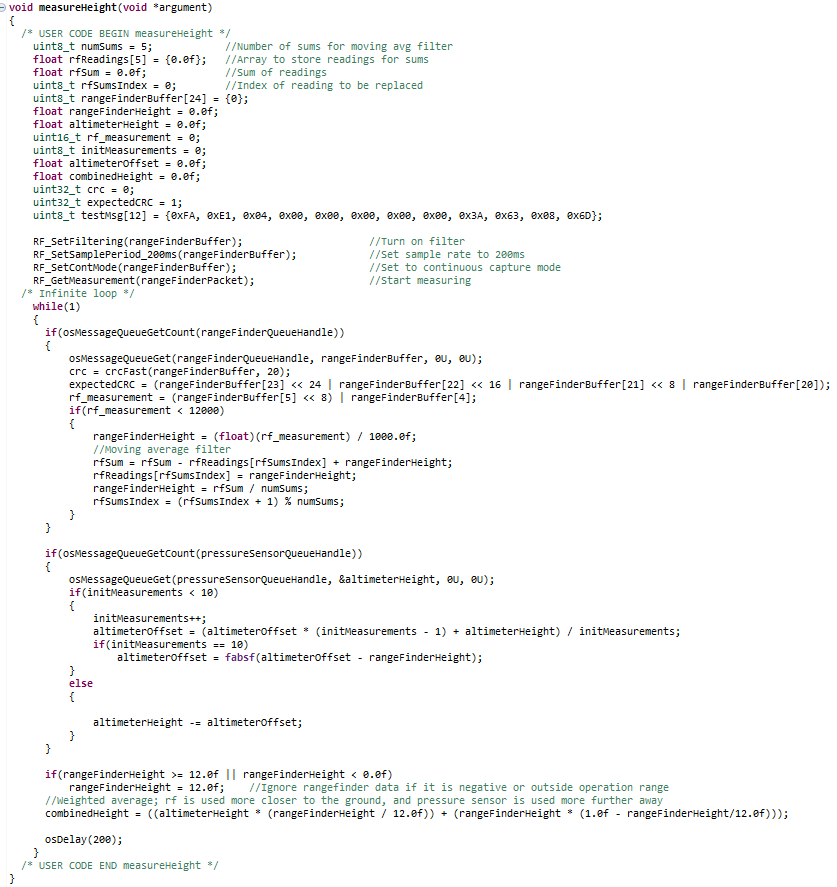
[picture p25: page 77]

Figure 44: Measure Height Task Code

## References

[1] “DJI Air 2S - all in one,” DJI, https://www.dji.com/de/air-2s (accessed May 26, 2023).
[2] “Exo X7 Ranger Plus,” EXO Drones, https://exodrones.com/products/exo-x7-ranger-plus (accessed

May 26, 2023).

[3] “FHL-LD19 12meter lidar - 30k lux,” youyeetoo wiki, https://wiki.youyeetoo.com/en/Lidar/D300

(accessed Dec. 11, 2023).

[4] J. Strickland, “What is a gimbal -- and what does it have to do with NASA?,” HowStuffWorks,

https://science.howstuffworks.com/gimbal.htm (accessed Dec. 11, 2023).

[5] Phil's Lab. PID Controller Implementation in Software - Phil's Lab #6. (May 22, 2020). Accessed: Dec. 12,

2023. [Online Video]. Available: https://www.youtube.com/watch?v=zOByx3Izf5U

[6] Phil's Lab. Extended Kalman Filter Software Implementation – Sensor Fusion #4 - Phil's Lab #3. (Aug 22,

2022). Accessed: Dec. 12, 2023. [Online Video]. Available:

https://www.youtube.com/watch?v=7HVPjkWOrLE

[7] Phil's Lab. Extended Kalman Filter Software Implementation - Sensor Fusion #4 - Phil's Lab #73 (Aug. 22,

2022). Accessed: Feb. 27, 2024. [Online Video]. Available:

https://www.youtube.com/watch?v=7HVPjkWOrLE

[8] Phil's Lab. FIR Filter Design and Software Implementation - Phil's Lab #17. (Dec. 20, 2020). Accessed:

Feb. 27, 2024. [Online Video]. Available: https://www.youtube.com/watch?v=uNNNj9AZisM

[9] ardnew, “Ili9341-STM32-hal,” GitHub, https://github.com/ardnew/ILI9341-STM32-HAL (accessed

Feb. 27, 2024).

[10] bao-eng, “BMI088-STM32,” GitHub, https://github.com/bao-eng/BMI088-STM32 (accessed Feb. 27,

2024).

[11] E. Seok, “stm32_hal_dshot,” GitHub, https://github.com/mokhwasomssi/stm32_hal_dshot

(accessed Feb. 27, 2024).

[12] E. Seok, “stm32_hal_nrf24l01p,” GitHub, https://github.com/mokhwasomssi/stm32_hal_nrf24l01p

(accessed Feb. 27, 2024).

[13] “ICP-10111 Datasheet.” InvenSense, San Jose, 2021.
[14] P. Salmony, “HADES Flight Control System,” GitHub,

https://github.com/pms67/HadesFCS/tree/master (accessed Feb. 27, 2024).

[15] “Grove - 6-axis accelerometer&gyroscope(bmi088): Seeed studio wiki,” Seeed Studio Wiki RSS,

https://wiki.seeedstudio.com/Grove-6-Axis_Accelerometer&Gyroscope_BMI088/ (accessed Mar.

16, 2024).

[16] “nRF24L01+ Single Chip 2.4GHz Transceiver Product Specification v1.0.” Nordic Semiconductor,

Trondheim, 2008.

[17] “STM32H755xI.” STMicroelectronics, Santa Clara, 2023.
[18] “a-Si TFT LCD Single Chip Driver 240RGBx320 Resolution and 262K color Specification.” ILI

Technology Corp., Zhubei, 2011.

[19] “BMI088: Data Sheet.” Bosch, Sunnyvale, 2022.
[20] “SpeedyBee BLS 50A 30×30 Stack User Manual.” Zhuhai KuaiFeng Technology Co., Zhuhai, 2022.

[21] D. Fox, W. Burgard, and S. Thrun, “The dynamic window approach to collision avoidance,” Carnegie

Mellon University: Robotics Institute,

https://www.ri.cmu.edu/pub_files/pub1/fox_dieter_1997_1/fox_dieter_1997_1.pdf (accessed

Mar. 14, 2024).

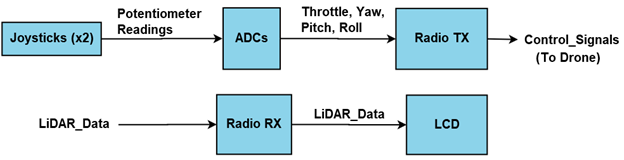
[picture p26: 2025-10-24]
Schematics/Controller System Block Diagram.png

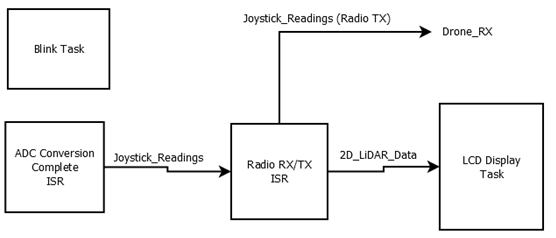
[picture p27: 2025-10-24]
Schematics/Controller Task Diagram.png

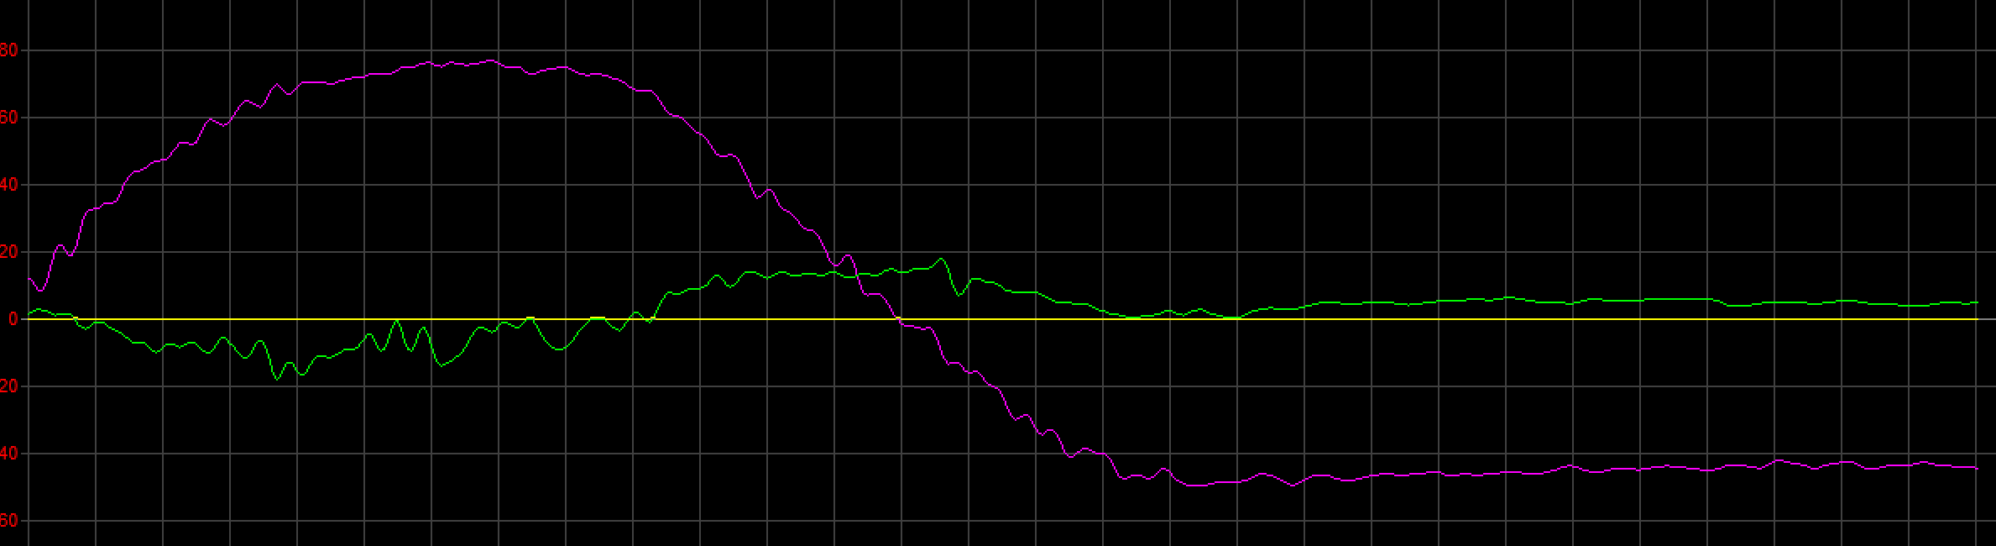
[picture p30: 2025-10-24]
Other Stuff/IMU G - roll M - pitch.png

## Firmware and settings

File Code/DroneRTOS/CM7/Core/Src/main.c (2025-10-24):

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
/* Includes ------------------------------------------------------------------*/
#include "main.h"
#include "cmsis_os.h"
#include "dma.h"
#include "eth.h"
#include "i2c.h"
#include "spi.h"
#include "tim.h"
#include "usart.h"
#include "usb_otg.h"
#include "gpio.h"

/* USER CODE BEGIN Includes */
#include "nrf24l01p.h"
#include "dshot.h"
#include "bmi088_stm32.h"
#include "bmi08x.h"
#include "bmi088.h"
#include "../DebugRedirect/retarget.h"
#include "../FlightController/flightcontroller.h"
/* USER CODE END Includes */

/* USER CODE BEGIN PD */

#define JS_DEADZONE 40

#ifndef HSEM_ID_0
#define HSEM_ID_0 (0U) /* HW semaphore 0*/
#endif

/* USER CODE END PD */


/* USER CODE BEGIN PV */
uint8_t RadioTX[32] = {0};
uint8_t RadioRX[32] = {0};
uint8_t bmi_init = 0;
uint8_t lidarPacket[47] = {0};
uint8_t rangeFinderPacket[24] = {0};
uint8_t firstMotorValsFlag = 1;
//uint16_t motors[4] = {0,0,0,0};

extern osMessageQueueId_t DShotQueueHandle;
extern osMessageQueueId_t motorControlQueueHandle;
extern osMessageQueueId_t lidarQueueHandle;
extern osMessageQueueId_t rangeFinderQueueHandle;
//extern motor_values;
/* USER CODE END PV */

void SystemClock_Config(void);
void PeriphCommonClock_Config(void);
void MX_FREERTOS_Init(void);
/* USER CODE BEGIN PFP */
void HAL_GPIO_EXTI_Callback(uint16_t GPIO_Pin);
void HAL_UART_RxCpltCallback(UART_HandleTypeDef *huart);
/* USER CODE END PFP */

/**
  * @brief  The application entry point.
  * @retval int
  */
int main(void)
{
/* USER CODE BEGIN Boot_Mode_Sequence_0 */
  int32_t timeout;
/* USER CODE END Boot_Mode_Sequence_0 */

/* USER CODE BEGIN Boot_Mode_Sequence_1 */
  /* Wait until CPU2 boots and enters in stop mode or timeout*/
  timeout = 0xFFFF;
  while((__HAL_RCC_GET_FLAG(RCC_FLAG_D2CKRDY) != RESET) && (timeout-- > 0));
  if ( timeout < 0 )
  {
  //Error_Handler();
  }
/* USER CODE END Boot_Mode_Sequence_1 */
  /* MCU Configuration--------------------------------------------------------*/

  /* Reset of all peripherals, Initializes the Flash interface and the Systick. */
  HAL_Init();

  /* Configure the system clock */
  SystemClock_Config();

/* Configure the peripherals common clocks */
  PeriphCommonClock_Config();
/* USER CODE BEGIN Boot_Mode_Sequence_2 */
/* When system initialization is finished, Cortex-M7 will release Cortex-M4 by means of
HSEM notification */
/*HW semaphore Clock enable*/
__HAL_RCC_HSEM_CLK_ENABLE();
/*Take HSEM */
HAL_HSEM_FastTake(HSEM_ID_0);
/*Release HSEM in order to notify the CPU2(CM4)*/
HAL_HSEM_Release(HSEM_ID_0,0);
/* wait until CPU2 wakes up from stop mode */
timeout = 0xFFFF;
while((__HAL_RCC_GET_FLAG(RCC_FLAG_D2CKRDY) == RESET) && (timeout-- > 0));
if ( timeout < 0 )
{
//Error_Handler();
}
/* USER CODE END Boot_Mode_Sequence_2 */

  /* Initialize all configured peripherals */
  MX_GPIO_Init();
  MX_DMA_Init();
  MX_USART3_UART_Init();
  MX_USB_OTG_FS_PCD_Init();
  MX_SPI2_Init();
  MX_TIM3_Init();
  MX_TIM4_Init();
  MX_ETH_Init();
  MX_USART1_UART_Init();
  MX_SPI3_Init();
  MX_I2C1_Init();
  MX_UART5_Init();
  MX_SPI6_Init();
  MX_I2C2_Init();
  MX_TIM6_Init();
  MX_TIM7_Init();
  /* USER CODE BEGIN 2 */
  RetargetInit(&huart3);
  nrf24l01p_tx_init(2500, _2Mbps);//May want to change to 2Mbps
  HAL_UART_Receive_DMA(&huart1, lidarPacket, 47);
  dshot_init(DSHOT600);
  BMI088_Init();

  HAL_Delay(100); //Delay for radio and any other initialization

  HAL_GPIO_WritePin(LD19_PWR_GPIO_Port, LD19_PWR_Pin, GPIO_PIN_SET);//Turn on LD19 LiDAR
  /* USER CODE END 2 */

  /* Init scheduler */
  osKernelInitialize();  /* Call init function for freertos objects (in freertos.c) */
  MX_FREERTOS_Init();

  /* Start scheduler */
  osKernelStart();
  /* We should never get here as control is now taken by the scheduler */
  /* Infinite loop */
  /* USER CODE BEGIN WHILE */
  while (1)
  {
    /* USER CODE END WHILE */

    /* USER CODE BEGIN 3 */
  }
  /* USER CODE END 3 */
}

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
/* USER CODE BEGIN 4 */
void HAL_GPIO_EXTI_Callback(uint16_t GPIO_Pin)
{
	motor_values motor_vals = {0,0,0,0};
	uint8_t status = 0;
	//TX
	//HAL_GPIO_TogglePin(GPIOB, GPIO_PIN_0);
	if(GPIO_Pin == NRF24L01P_IRQ_PIN_NUMBER)
	{
		//uint8_t addrs[5] = {};
		status = nrf24l01p_get_status();
		if((status & 0b00010000))//Check MAX_RT interrupt. Need to clear to enable comm.
		{
			nrf24l01p_clear_max_rt();

			if(htim7.Instance->CNT >= 3999)//Reset
			{
				//If radio disconnects, turn off motors -- Can be removed later, for flight testing low to gnd
				motor_vals.pitch = 0;
				motor_vals.roll = 0;
				motor_vals.yaw = 0;
				motor_vals.throttle = 0;
				osMessageQueuePut(motorControlQueueHandle, &motor_vals, 0U, 0U);

				nrf24l01p_clear_max_rt();
				nrf24l01p_reset_tx_addrs();
				nrf24l01p_flush_rx_fifo();
				nrf24l01p_flush_tx_fifo();
				//nrf24l01p_power_down();
				//nrf24l01p_power_up();
				nrf24l01p_tx_init(2500, _2Mbps);//Change init settings to match if they are ever changed
				osDelay(100);
				htim7.Instance->CNT = 0;
			}
		}
		else if(status & 0b01000000)//Check if RX_DR status bit is set. If it is set, there was an ack w/ payload. RX_DR and TX_DS should both be asserted in this case.
		{
			htim7.Instance->CNT = 0;
			nrf24l01p_read_rx_fifo(RadioRX, 16);//need to make sure payload length define is set correctly
			nrf24l01p_clear_rx_dr(); //Clear TX_DR interrupt flag

			//Force Throttle value to 0 or 47 depending on what ESC wants for 0 throttle
			motor_vals.pitch = (int16_t)(((RadioRX[0] << 8) | RadioRX[1]) - 1024);
			motor_vals.roll = (int16_t)(((RadioRX[2] << 8) | RadioRX[3]) - 1024);
			motor_vals.yaw = (int16_t)(((RadioRX[4] << 8) | RadioRX[5]) - 1024);
			motor_vals.throttle = ((RadioRX[6] << 8) | RadioRX[7]);

			//Only claculate and update motor controls if the values are reasonable. For some reason, the radio will receive very high values. May be an issue with the radio. Not sure.
			if(motor_vals.throttle < 2200 && abs(motor_vals.yaw) < 1200 && abs(motor_vals.pitch) < 1200 && abs(motor_vals.roll) < 1200)
			{
				//Deadzones
				if(motor_vals.throttle < (48 + JS_DEADZONE))
					motor_vals.throttle = 0;
				else if(motor_vals.throttle > MAX_THROTTLE)
					motor_vals.throttle = MAX_THROTTLE;

				if(motor_vals.yaw > -JS_DEADZONE && motor_vals.yaw < JS_DEADZONE)
					motor_vals.yaw = 0;

				if(motor_vals.roll > -JS_DEADZONE && motor_vals.roll < JS_DEADZONE)
					motor_vals.roll = 0;

				if(motor_vals.pitch > -JS_DEADZONE && motor_vals.pitch < JS_DEADZONE)
					motor_vals.pitch = 0;

				osMessageQueuePut(motorControlQueueHandle, &motor_vals, 0U, 0U);
			}
		}
		nrf24l01p_tx_irq(); // clear interrupt flag (TX_DS)

	}

}

void HAL_UART_RxCpltCallback(UART_HandleTypeDef *huart)
{
	if(huart == &huart1)
	{
		//HAL_UART_Receive_DMA(&huart1, lidarPacket, 47);
		//uint8_t dataValid = 1;
		osMessageQueuePut(lidarQueueHandle, lidarPacket, 0U, 0U);
	}
	else if(huart == &huart5)
	{
		if(rangeFinderPacket[1] == 0xE0)
			osMessageQueuePut(rangeFinderQueueHandle, rangeFinderPacket, 0U, 0U);
		//HAL_UART_Receive_DMA(&huart5, buffer, 24);
	}
}

/* USER CODE END 4 */

/**
  * @brief  Period elapsed callback in non blocking mode
  * @note   This function is called  when TIM1 interrupt took place, inside
  * HAL_TIM_IRQHandler(). It makes a direct call to HAL_IncTick() to increment
  * a global variable "uwTick" used as application time base.
  * @param  htim : TIM handle
  * @retval None
  */
void HAL_TIM_PeriodElapsedCallback(TIM_HandleTypeDef *htim)
{
  if (htim->Instance == TIM1) {
    HAL_IncTick();
  }
}

/**
  * @brief  This function is executed in case of error occurrence.
  * @retval None
  */
void Error_Handler(void)
{
  /* USER CODE BEGIN Error_Handler_Debug */
  /* User can add his own implementation to report the HAL error return state */
  __disable_irq();
  while (1)
  {
  }
  /* USER CODE END Error_Handler_Debug */
}

#ifdef  USE_FULL_ASSERT
/**
  * @brief  Reports the name of the source file and the source line number
  *         where the assert_param error has occurred.
  * @param  file: pointer to the source file name
  * @param  line: assert_param error line source number
  * @retval None
  */
void assert_failed(uint8_t *file, uint32_t line)
{
  /* USER CODE BEGIN 6 */
  /* User can add his own implementation to report the file name and line number,
     ex: printf("Wrong parameters value: file %s on line %d\r\n", file, line) */
  /* USER CODE END 6 */
}
#endif /* USE_FULL_ASSERT */

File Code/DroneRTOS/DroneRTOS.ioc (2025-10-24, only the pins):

Mcu.UserName=STM32H755ZITx
PA1.Signal=ETH_REF_CLK
PA11.Signal=USB_OTG_FS_DM
PA12.Signal=USB_OTG_FS_DP
PA2.Signal=ETH_MDIO
PA4.GPIO_Label=LD19_PWR
PA4.Signal=GPIO_Output
PA5.Signal=SPI6_SCK
PA6.Signal=S_TIM3_CH1
PA7.Signal=ETH_CRS_DV
PA8.Signal=USB_OTG_FS_SOF
PA9.Signal=USB_OTG_FS_VBUS
PB0.GPIO_Label=LD1 [Green Led]
PB0.Signal=GPIO_Output
PB1.Signal=S_TIM3_CH4
PB10.Signal=I2C2_SCL
PB11.Signal=I2C2_SDA
PB12.GPIO_Label=RF_RX
PB12.Signal=UART5_RX
PB13.Signal=ETH_TXD1
PB14.GPIO_Label=LD3 [Red Led]
PB14.Signal=GPIO_Output
PB15.Signal=USART1_RX
PB2.Signal=SPI3_MOSI
PB6.Signal=USART1_TX
PB7.Signal=I2C1_SDA
PB8.Signal=I2C1_SCL
PC1.Signal=ETH_MDC
PC10.Signal=SPI3_SCK
PC11.Signal=SPI3_MISO
PC12.GPIO_Label=RF_TX
PC12.Signal=UART5_TX
PC13.GPIO_Label=B1 [Blue PushButton]
PC13.Signal=GPIO_Input
PC2_C.Signal=SPI2_MISO
PC3_C.Signal=SPI2_MOSI
PC4.Signal=ETH_RXD0
PC5.Signal=ETH_RXD1
PC7.GPIO_Label=GYRO_INT
PC7.Signal=GPXTI7
PC8.GPIO_Label=ACC_INT
PC8.Signal=GPXTI8
PD10.GPIO_Label=USB_OTG_FS_PWR_EN
PD10.Signal=GPIO_Output
PD11.GPIO_Label=CE_NRF
PD11.Signal=GPIO_Output
PD13.Signal=S_TIM4_CH2
PD14.Signal=S_TIM4_CH3
PD3.Signal=SPI2_SCK
PD8.GPIO_Label=STLINK_RX
PD8.Signal=USART3_TX
PD9.GPIO_Label=STLINK_TX
PD9.Signal=USART3_RX
PE1.GPIO_Label=LD2 [Yellow Led]
PE1.Signal=GPIO_Output
PE3.GPIO_Label=SPI2_CSN
PE3.Signal=GPIO_Output
PE4.GPIO_Label=CS_GYRO
PE4.Signal=GPIO_Output
PE6.GPIO_Label=CS_ACC
PE6.Signal=GPIO_Output
PG11.Signal=ETH_TX_EN
PG12.Signal=SPI6_MISO
PG13.Signal=ETH_TXD0
PG14.Signal=SPI6_MOSI
PG6.GPIO_Label=NRF_INT
PG6.Signal=GPXTI6

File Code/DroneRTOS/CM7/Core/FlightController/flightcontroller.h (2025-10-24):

/*
 * flightcontroller.h
 *
 *  Created on: Nov 2, 2023
 *      Author: robin
 */

#ifndef FLIGHTCONTROLLER_FLIGHTCONTROLLER_H_
#define FLIGHTCONTROLLER_FLIGHTCONTROLLER_H_

#include "bmi08x_defs.h"
#include "math.h"
#include "../Filters/FIRFilter.h"
#include "../Filters/ExtendedKalmanFilter.h"
#include "pid.h"

#define PID_MULT 				4.0f
//For One-layer controllers:
//#define MAX_ROLL_ANGLE 		    25.0f * PID_MULT//Roll and Pitch are multiplied by 10, should control to +/- 35 deg
//#define MAX_PITCH_ANGLE 		25.0f * PID_MULT

//For two-layer controllers:
#define MAX_ROLL_ANGLE 		    25.0f
#define MAX_PITCH_ANGLE 		25.0f


#define MAX_ROLL_RATE		    120.0f
#define MAX_PITCH_RATE  		120.0f
#define MAX_YAW_RATE 		    120.0f
#define ANGLE_TO_RATE_CONV		(MAX_ROLL_RATE / MAX_ROLL_ANGLE)
#define MAX_THROTTLE	        1647 //(.8 * 2000) + 48 (max throttle = 2047, min = 48).
							 	 	 //Gives 20% throttle to work with for PID control
#define MAX_JOYSTICK_VAL 		1024.0f

#define ALPHA 			0.05F
#define GRAVITY 		9.8067F
#define PI				3.141592654F
#define RAD_TO_DEG		57.29577951F//((float)(180/PI))
#define DEG_TO_RAD		(float)(PI/180.0F) //PI/180

typedef struct
{
	uint16_t throttle;
	int16_t yaw;
	int16_t pitch;
	int16_t roll;

}motor_values;

typedef struct
{
	int16_t motor1;
	int16_t motor2;
	int16_t motor3;
	int16_t motor4;

}DShotVals;

typedef struct
{
	float yaw;
	float pitch;
	float roll;
	float rollRate;
	float pitchRate;
	float yawRate;
}DroneRotations;



#endif /* FLIGHTCONTROLLER_FLIGHTCONTROLLER_H_ */

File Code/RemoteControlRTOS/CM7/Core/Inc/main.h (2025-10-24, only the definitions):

#define SPI2_CSN_Pin GPIO_PIN_3
#define SPI2_CSN_GPIO_Port GPIOE
#define B1_Pin GPIO_PIN_13
#define B1_GPIO_Port GPIOC
#define LCD_SCK_Pin GPIO_PIN_5
#define LCD_SCK_GPIO_Port GPIOA
#define LD1_Pin GPIO_PIN_0
#define LD1_GPIO_Port GPIOB
#define LD3_Pin GPIO_PIN_14
#define LD3_GPIO_Port GPIOB
#define STLINK_RX_Pin GPIO_PIN_8
#define STLINK_RX_GPIO_Port GPIOD
#define STLINK_TX_Pin GPIO_PIN_9
#define STLINK_TX_GPIO_Port GPIOD
#define CE_NRF_Pin GPIO_PIN_11
#define CE_NRF_GPIO_Port GPIOD
#define NRF_INT_Pin GPIO_PIN_6
#define NRF_INT_GPIO_Port GPIOG
#define NRF_INT_EXTI_IRQn EXTI9_5_IRQn
#define LCD_MOSI_Pin GPIO_PIN_7
#define LCD_MOSI_GPIO_Port GPIOD
#define LCD_MISO_Pin GPIO_PIN_9
#define LCD_MISO_GPIO_Port GPIOG
#define Red_LED_Pin GPIO_PIN_11
#define Red_LED_GPIO_Port GPIOG
#define Green_LED_Pin GPIO_PIN_13
#define Green_LED_GPIO_Port GPIOG
#define LCD_CS_Pin GPIO_PIN_5
#define LCD_CS_GPIO_Port GPIOB
#define LCD_DC_Pin GPIO_PIN_6
#define LCD_DC_GPIO_Port GPIOB
#define LCD_RESET_Pin GPIO_PIN_7
#define LCD_RESET_GPIO_Port GPIOB
#define LD2_Pin GPIO_PIN_1
#define LD2_GPIO_Port GPIOE

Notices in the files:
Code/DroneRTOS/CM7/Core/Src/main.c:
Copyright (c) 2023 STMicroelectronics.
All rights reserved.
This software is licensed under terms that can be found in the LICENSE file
